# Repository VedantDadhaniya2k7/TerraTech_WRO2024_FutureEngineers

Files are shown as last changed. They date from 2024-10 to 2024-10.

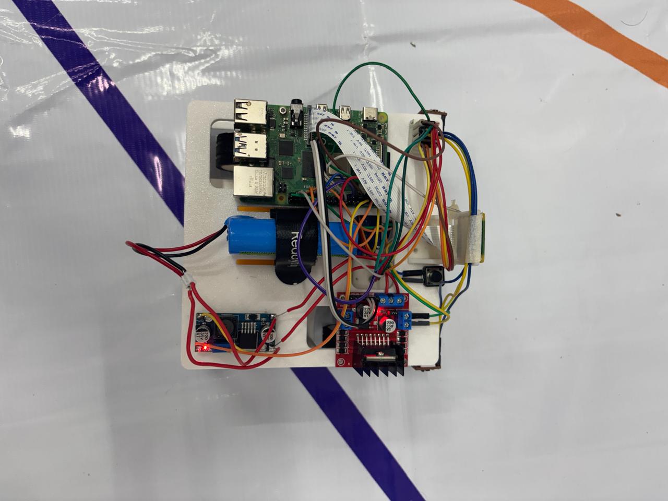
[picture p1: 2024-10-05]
Vehicle_photos/Top_view.jpg

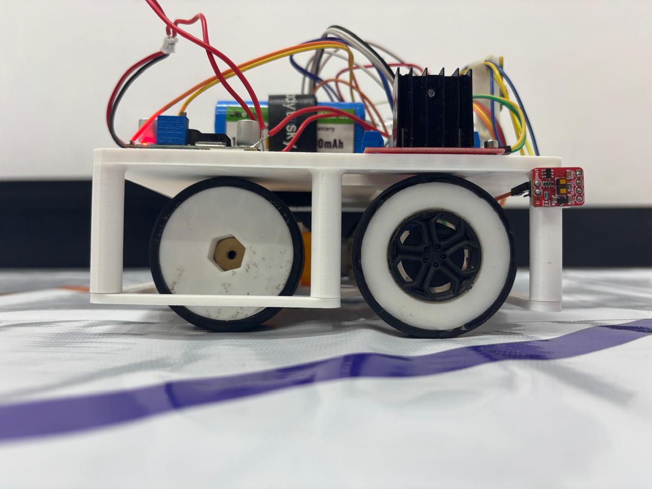
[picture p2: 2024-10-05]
Vehicle_photos/Left_view.jpg

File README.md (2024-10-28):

WRO 2024 Future Engineers - Team TerraTech (Team code: 1844)
====

This repository contains engineering materials of the self-driven vehicle of Team TerraTech participating in the WRO Future Engineers competition in the season 2024.

## Content

* `Documentation` contains an Engineering Document describing our Robot, Its components, Why we selected each Component, Code, and, its implementation.
* `Team_Photos` contains photos of the team (an official one and one funny photo with all team members)
* `Vehicle_Photos` contains photos of the vehicle (from every side, from top and bottom)
* `Video` contains videos that demonstrate the robot's functionality including it completing 3 laps of the Open Challenge
* `Schematics` contains schematic diagrams of each electromechanical components (electronic components and motors) used in the vehicle and how they connect to each other and RaspberryPi and also one schematic with the complete circuit connections shown
* `Source_code` contains code of control software for all components which were programmed to participate in the competition
* `3D_models` contains the files for models used by 3D printers, laser cutting machines and CNC machines to produce the vehicle elements. It contains the files in both STL and gcode format
* `Component_tests` contains code for testing and making sure each component of the whole robot is functional. Includes test codes for servo motor, rear motors, camera recognition, as well as the vl53l1x distance measurement sensor

## Introduction

### Team Introduction


_**Vedant Dadhaniya** (Left Side) - Team Lead, Head of Programming and 3-D Design_

Vedant is a STEM enthusiast who has recurringly been participating in the World Robot Olympiad since 2019 and this is his 4th time participating for it. He began by playing with jigsaw puzzles when he developed interest in LEGO which soon led to introduction to the world of robotics through EV3. Over the years, he has developed many skills in robotics including 3D part designing, electrical wiring, and languages such as Python, C#, HTML/CSS, and Java. He brings his computer vision skills with Raspberry Pi which he had worked on during the COVID Pandemic. He is an avid reader and also likes to play the guitar.

_**Devansh Harivallabhdas** (Right Side) - Head of Hardware and 3-D Printing_ 

Devansh is a Robotics and stem enthusiast from Ahmedabad. It is his first time at World Robot Olympiad. He is 14 and studies in class 9. As a child , Lego building was his favourite activity . He discovered his love for wires , motors and circuits in the Covid lockdown 4 years ago. Ever since he is pursuing it . He also has keen interest in Environmental applications ,Physics and chemistry and a passionate urban farmer. His dream is to create technologies and solutions that can impact the conservation of our environment.

### Reason for choosing the team name _TerraTech_

Terra is Latin for the word earth , since the theme for this WRO is Earth Allies. And Tech as we all know is the shortform of the word technology.

## About the Project

### Open Challenge Working Idea



## How to replicate the robot

First collect all the parts required as mentioned in our [Engineering document](http://bit.ly/3C0usWp)
and print all the parts as given in the `3D_models` folder of this repository

Now assemble all the 3d printed parts and the electromechanical components such that the fundamental component assembly looks like this:

Robot design

Then connect the jumper cables as per the following electrical circuit diagram:

Electrical diagram

Before booting the RaspberryPi 4b, flash a 32GB microSD card with a Bookworm image and insert it into the microSD card slot of the RaspberryPi
Now load the Source code onto the raspberry pi using USB to USB communication or a portable data storage device.

Now in the terminal of the RaspberryPi, setup a virtual environment as such:

```> python3 -m venv <give a name to your virtual environment>```

Activate the virtual environment using the following command:

```> source <name of virtual environment>/bin/activate```

Now install the following libraries using ```> pip install <library name>``` :

* opencv-python
* adafruit-circuitpython-vl53l1x
* board
* digitalio
* numpy

Now the robot is ready to run

# References

* https://learn.adafruit.com/adafruit-vl53l1x/python-circuitpython
* https://learn.sparkfun.com/tutorials/qwiic-distance-sensor-vl53l1x-hookup-guide/python-examples
* https://docs.sunfounder.com/projects/raphael-kit/en/latest/appendix/install_the_libraries.html#create-virtual
* https://docs.sunfounder.com/projects/raphael-kit/en/latest/appendix/i2c_configuration.html#i2c-config
* https://www.youtube.com/watch?v=2bganVdLg5Q&t=42s
* https://github.com/World-Robot-Olympiad-Association/wro2022-fe-template
* https://www.youtube.com/playlist?list=PLGs0VKk2DiYyXlbJVaE8y1qr24YldYNDm

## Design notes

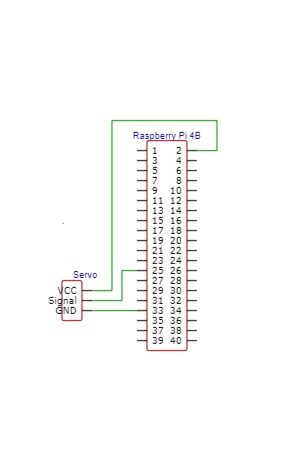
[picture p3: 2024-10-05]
Schematics/Circuit Diagrams/Servo_schematic.jpg

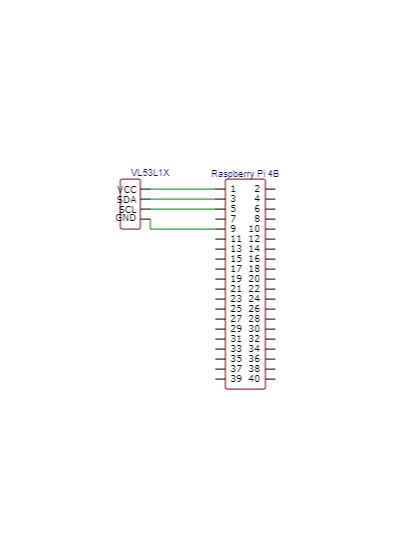
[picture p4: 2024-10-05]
Schematics/Circuit Diagrams/VL53L1X_schematic.jpg

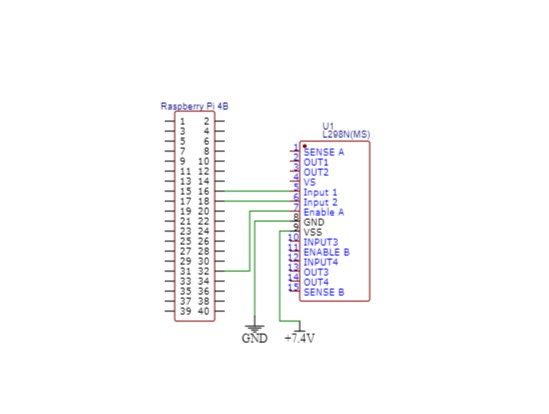
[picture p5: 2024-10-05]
Schematics/Circuit Diagrams/L298N_schematic.jpg

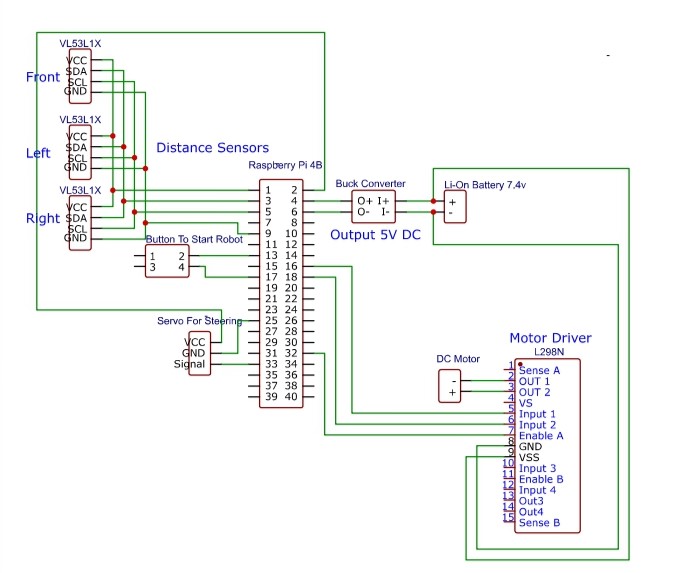
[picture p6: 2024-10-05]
Schematics/Circuit Diagrams/Overall_circuit.jpg

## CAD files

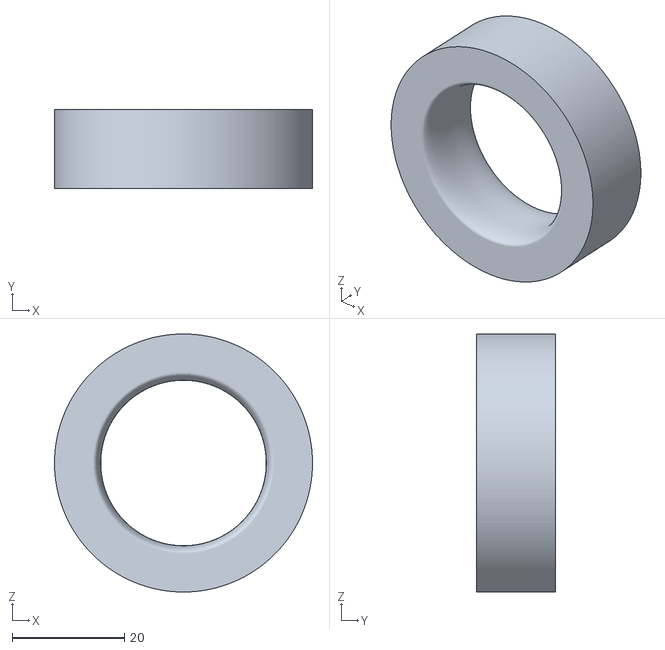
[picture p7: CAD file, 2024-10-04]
3D_models/STL/wheel_front.stl
46.0 x 14.0 x 46.0

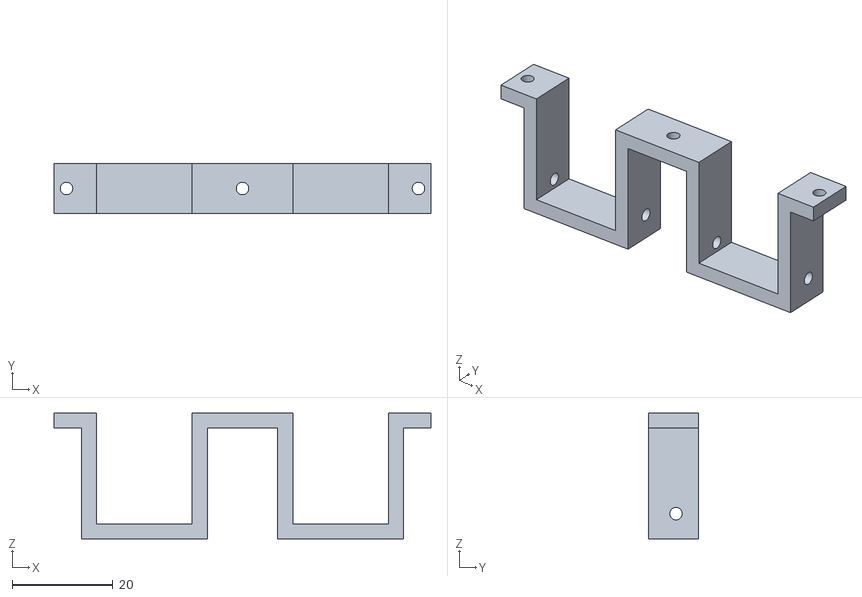
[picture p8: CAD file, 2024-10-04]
3D_models/STL/rear_motor_bracket.stl
75.0 x 10.0 x 25.0

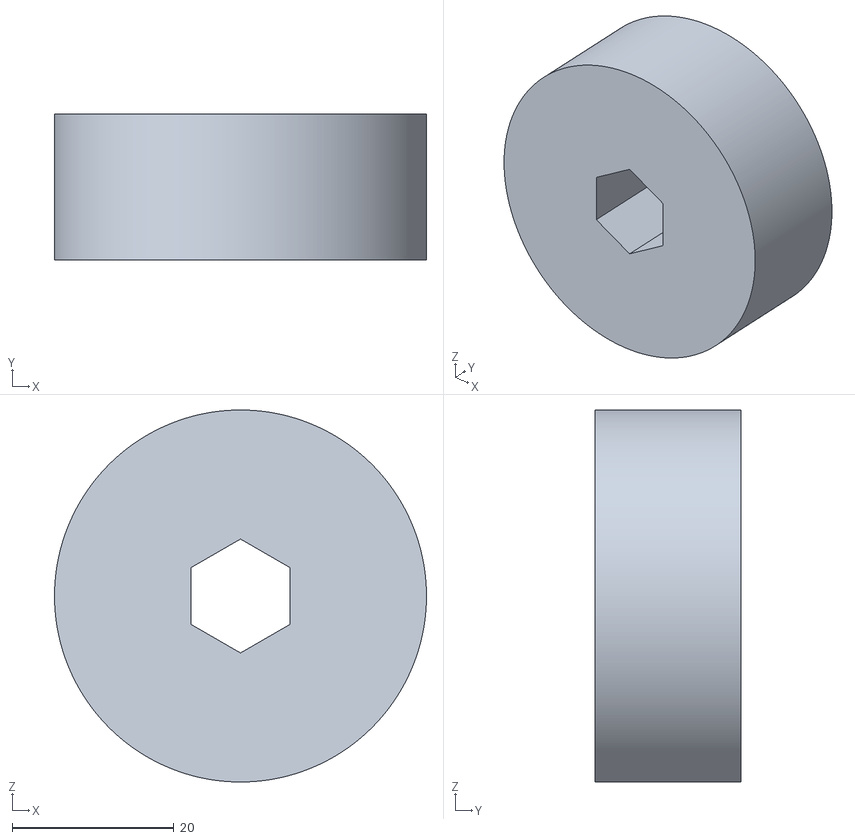
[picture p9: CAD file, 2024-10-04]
3D_models/STL/wheel_rear.stl
46.0 x 18.0 x 46.0

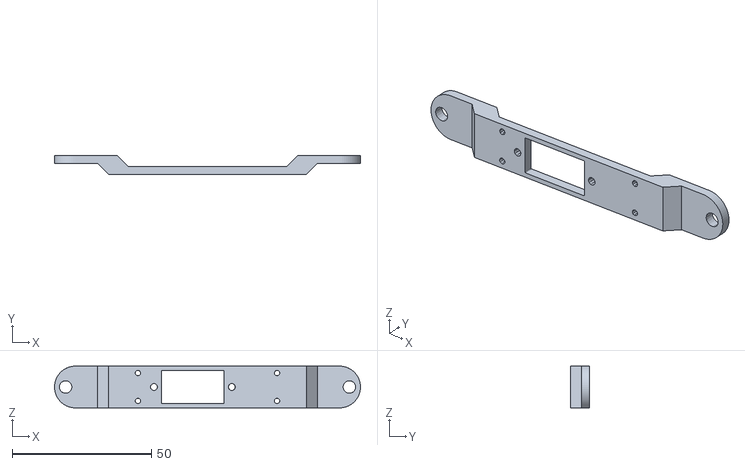
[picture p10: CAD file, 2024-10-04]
3D_models/STL/servo_mount.stl
110.0 x 7.00 x 15.0

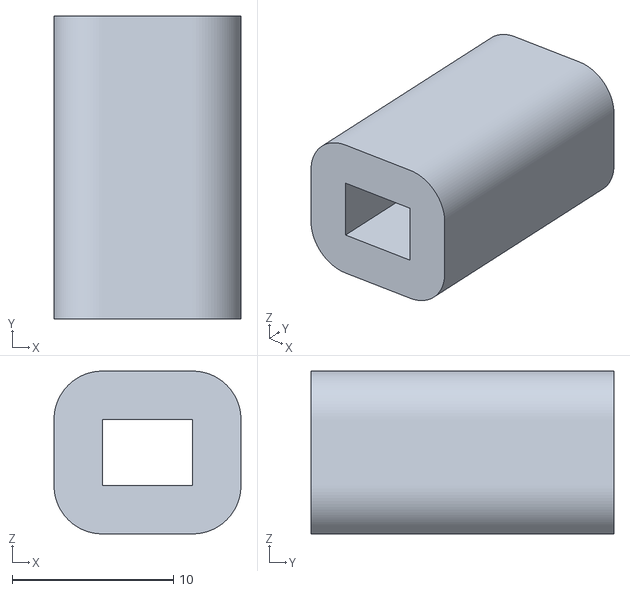
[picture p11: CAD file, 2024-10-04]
3D_models/STL/rear_motor_coupling.stl
11.6 x 18.8 x 10.1

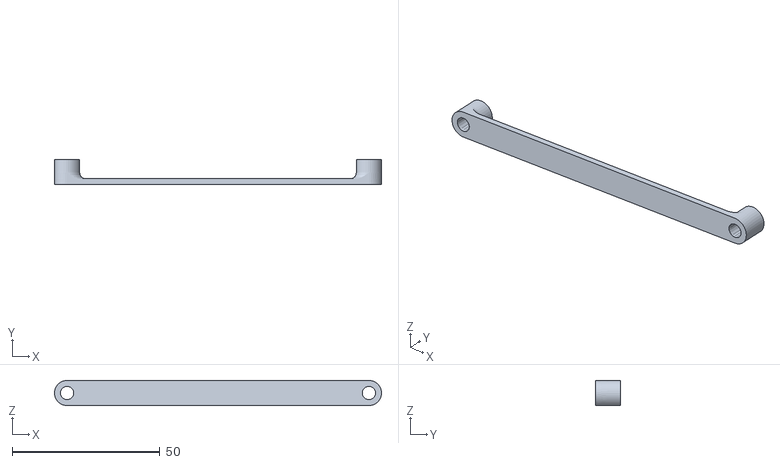
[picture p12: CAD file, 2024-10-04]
3D_models/STL/steering_rod.stl
110.5 x 8.50 x 8.50

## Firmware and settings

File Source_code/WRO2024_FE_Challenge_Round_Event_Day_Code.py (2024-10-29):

"""
Trying to use shape detection to locate red or green block, show the closest one and print() the no. of pillars detected while autosaving the hsv ranges
(P.S. This version of the code is for RaspberryPi not PC)
"""



"""
IMPORTS
"""
import time
time.sleep(5)
import cv2
import math
import numpy as np
from picamera2 import Picamera2
import RPi.GPIO as GPIO
import board
import digitalio
import adafruit_vl53l1x


in1 = 23
in2 = 24
en = 12
servo = 13
SHUT1 = 5
SHUT2 = 6
SHUT3 = 26


"""
GPIO SETUP
"""
GPIO.setwarnings(False)
GPIO.setmode(GPIO.BCM)
GPIO.setup(in1    , GPIO.OUT)
GPIO.setup(in2    , GPIO.OUT)
GPIO.setup(en     , GPIO.OUT)
GPIO.setup(servo  , GPIO.OUT)
GPIO.output(in1   , GPIO.LOW)
GPIO.output(in2   , GPIO.LOW)


motor  = GPIO.PWM(   en, 1000)
servo1 = GPIO.PWM(servo,   50) 
motor.start(100)
motor.ChangeDutyCycle(50)
servo1.start(0)

i2c = board.I2C()
"""
ToF SHUT PIN SETUP
"""
shut_1 = digitalio.DigitalInOut(board.D5 )
shut_2 = digitalio.DigitalInOut(board.D6 )
shut_3 = digitalio.DigitalInOut(board.D26)
shut_1.switch_to_output(value=False)
shut_2.switch_to_output(value=False)
shut_3.switch_to_output(value=False)
"""
ToF SETUP and ADDRESS REASSIGNMENT
"""
#sensor 1
shut_1.value        = True
tof_1               = adafruit_vl53l1x.VL53L1X(i2c)
tof_1.distance_mode = 2
tof_1.timing_budget = 100
tof_1.set_address(0x28)
tof_1.start_ranging()
#sensor 2
shut_2.value        = True
tof_2               = adafruit_vl53l1x.VL53L1X(i2c)
tof_2.distance_mode = 2
tof_2.timing_budget = 100
tof_2.set_address(0x38)
tof_2.start_ranging()
#sensor 3
shut_3.value        = True
tof_3               = adafruit_vl53l1x.VL53L1X(i2c)
tof_3.distance_mode = 2
tof_3.timing_budget = 100
tof_3.set_address(0x48)
tof_3.start_ranging()



"""
Pi Cam Setup
"""
p=Picamera2()

WIDTH = 1280   
HEIGHT = 720

p.preview_configuration.main.size=(WIDTH,HEIGHT)
p.preview_configuration.main.format='RGB888'
p.preview_configuration.align()
p.configure('preview')

p.start()



"""
FUNCTIONS
"""

#* empty fuction
def empty(a):
    pass

#* draws shape and bounding box aroung a countour of sufficient area
def getContours(img, imgContour, clr):
    contours, hierarchy = cv2.findContours(img, cv2.RETR_EXTERNAL, cv2.CHAIN_APPROX_NONE)

    count = 0
    pillars = []
    correct_directions = []

    # draw vert. lines 
    cv2.line(imgContour, (int(WIDTH/3), 0), (int(WIDTH/3), HEIGHT), (0, 255, 255), 1)
    cv2.line(imgContour, (int(2*WIDTH/3), 0), (int(2*WIDTH/3), HEIGHT), (0, 255, 255), 1)
    
    cv2.line(imgContour, ( 291, 720), (679, 419), (0, 255, 255), 1)
    cv2.line(imgContour, (1110, 720), (679, 419), (0, 255, 255), 1)

    for cnt in contours:
        area = cv2.contourArea(cnt)
        area_thresh = cv2.getTrackbarPos("AreaThresh", "Parameters")
        if area >= area_thresh:
            count += 1

            cv2.drawContours(imgContour, cnt, -1, (255, 0, 255), 2)
            
            peri = cv2.arcLength(cnt, True)
            appx = cv2.approxPolyDP(cnt, 0.02*peri, True)
            
            x, y, w, h = cv2.boundingRect(appx) # x: x-coordinate of top left corner of bb, y: y-coordinate of top left corner of bb, w: width , h: height
                
            if y > 355:
                coords = [(x, y), (x+w, y), (x, y+h), (x+w, y+h)]
                pillars.append(coords)
                drawn = False
                
                for i,j in coords:
                    if i < (2*WIDTH/3) and clr == 'green':
                        cv2.rectangle(imgContour, (x, y), (x+w, y+h), (0, 0, 255), 3)
                        drawn = True
                    elif i > (WIDTH/3) and clr == 'red':
                        cv2.rectangle(imgContour, (x, y), (x+w, y+h), (0, 0, 255), 3)
                        drawn = True
                if drawn == False:
                    cv2.rectangle(imgContour, (x, y), (x+w, y+h), (0, 255, 0), 3) 
    
                # area is inversly proporsional to square of dist
                # at 30cm dist -> area = 64000
                dist = 30/math.sqrt(area/32100)
    
                cv2.putText(imgContour, "x: " + str(x) + ', y: ' + str(y) + ', w: ' + str(w) + ', h: ' + str(h), (x, y - 70), cv2.FONT_HERSHEY_COMPLEX, 0.7, (0, 255, 0), 2)
                
                asdfg = (0, 0, 255) if (((((137*(x+w))+(177*(y+h))-167362>0) or (x+w > 679.6))and(clr == 'red')) or ((((-192*(x+w))+(275*(y+h))+15120>0) or (x+w < 679.6))and(clr=='green'))) else (0, 255, 0)
                correct_dir = True if asdfg == (0, 255, 0) else False
                correct_directions.append(correct_dir)
                cv2.putText(imgContour, "Area" + str(int(area)), (x, y - 45), cv2.FONT_HERSHEY_COMPLEX, 0.7, asdfg, 2)
                cv2.putText(imgContour, "Dist" + str(int(dist)), (x, y - 20), cv2.FONT_HERSHEY_COMPLEX, 0.7, asdfg, 2)

    return count, pillars, correct_directions



"""
LOAD MASK DATA
"""
with open('green_mask.txt', 'r') as gm:
    g_hmin, g_hmax, g_smin, g_smax, g_vmin, g_vmax = gm.read().split(' ')

with open('red_mask.txt', 'r') as rm:
    r_hmin, r_hmax, r_smin, r_smax, r_vmin, r_vmax = rm.read().split(' ')

first_round = True
"""
TRACKBARS SETUP
"""
cv2.namedWindow("Green HSV dials")
cv2.resizeWindow("Green HSV dials", 640, 270)
cv2.createTrackbar("HUE Min", "Green HSV dials", int(g_hmin), 179, empty)
cv2.createTrackbar("HUE Max", "Green HSV dials", int(g_hmax), 179, empty)
cv2.createTrackbar("SAT Min", "Green HSV dials", int(g_smin), 255, empty)
cv2.createTrackbar("SAT Max", "Green HSV dials", int(g_smax), 255, empty)
cv2.createTrackbar("VAL Min", "Green HSV dials", int(g_vmin), 255, empty)
cv2.createTrackbar("VAL Max", "Green HSV dials", int(g_vmax), 255, empty)
cv2.createTrackbar("Start detection", "Green HSV dials", 1, 1, empty)

cv2.namedWindow("Red HSV dials")
cv2.resizeWindow("Red HSV dials", 640, 270)
cv2.createTrackbar("HUE Min", "Red HSV dials", int(r_hmin), 179, empty)
cv2.createTrackbar("HUE Max", "Red HSV dials", int(r_hmax), 179, empty)
cv2.createTrackbar("SAT Min", "Red HSV dials", int(r_smin), 255, empty)
cv2.createTrackbar("SAT Max", "Red HSV dials", int(r_smax), 255, empty)
cv2.createTrackbar("VAL Min", "Red HSV dials", int(r_vmin), 255, empty)
cv2.createTrackbar("VAL Max", "Red HSV dials", int(r_vmax), 255, empty)

cv2.namedWindow("Parameters")
cv2.resizeWindow("Parameters", 640, 120)
cv2.createTrackbar("THRESH_2", "Parameters", 10, 255, empty)
cv2.createTrackbar("THRESH_1", "Parameters", 20, 255, empty)
cv2.createTrackbar("AreaThresh", "Parameters", 650, 5000, empty)

btn = 27
led = 16
cmd_given = False
GPIO.setup(led ,GPIO.OUT)
GPIO.setup(btn ,GPIO.IN)
GPIO.output(led  ,GPIO.HIGH)
"""
WAIT FOR BTN ACTIVATION
"""
start= time.time()
print("Awaiting command")
while not cmd_given:
    if GPIO.input(btn) == GPIO.HIGH:
        cur = time.time() - start
    else:
        cur = 0
        start = time.time()
    if cur > 0.5:
        cmd_given = True

GPIO.output(led  ,GPIO.LOW)
time.sleep(1)
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

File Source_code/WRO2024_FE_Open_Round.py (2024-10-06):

import RPi.GPIO as GPIO # type: ignore
import time
import board # type: ignore
import digitalio # type: ignore
import adafruit_vl53l1x # type: ignore

"""
GPIO PINS
"""
btn         = 27
en          = 12
in1         = 23
in2         = 24
servo       = 13
"""
DATA VARIABLES
"""
cur         = 0
lap_counter = 0
turn_dir    = 0
cmd_given   = False
"""
GPIO SETUP
"""
GPIO.setwarnings(False)
GPIO.setmode(GPIO.BCM)
GPIO.setup(in1   ,GPIO.OUT)
GPIO.setup(in2   ,GPIO.OUT)
GPIO.setup(en    ,GPIO.OUT)
GPIO.setup(servo ,GPIO.OUT)
GPIO.output(in1  ,GPIO.LOW)
GPIO.output(in2  ,GPIO.LOW)
GPIO.setup(btn   , GPIO.IN)
"""
PWM SETUP
"""
mpower = GPIO.PWM(en   ,1000)
servo1 = GPIO.PWM(servo,  50) 
"""
I2C SETUP
"""
i2c = board.I2C()
"""
ToF SHUT PIN SETUP
"""
shut_1 = digitalio.DigitalInOut(board.D5 )
shut_2 = digitalio.DigitalInOut(board.D6 )
shut_3 = digitalio.DigitalInOut(board.D26)
shut_1.switch_to_output(value=False)
shut_2.switch_to_output(value=False)
shut_3.switch_to_output(value=False)
"""
ToF SETUP and ADDRESS REASSIGNMENT
"""
#sensor 1
shut_1.value        = True
tof_1               = adafruit_vl53l1x.VL53L1X(i2c)
tof_1.distance_mode = 2
tof_1.timing_budget = 100
tof_1.set_address(0x28)
#sensor 2
shut_2.value        = True
tof_2               = adafruit_vl53l1x.VL53L1X(i2c)
tof_2.distance_mode = 2
tof_2.timing_budget = 100
tof_2.set_address(0x38)
#sensor 3
shut_3.value        = True
tof_3               = adafruit_vl53l1x.VL53L1X(i2c)
tof_3.distance_mode = 2
tof_3.timing_budget = 100
tof_3.set_address(0x48)


"""
WAIT FOR BTN ACTIVATION
"""
start= time.time()
print("Awaiting command")
while not cmd_given:
    if GPIO.input(btn) == GPIO.HIGH:
        cur = time.time() - start
    else:
        cur = 0
        start = time.time()
    if cur > 0.5:
        cmd_given = True
time.sleep(1)
"""
BTN ACTIVATED
"""


"""
START DETECTING
"""
tof_1.start_ranging()
tof_2.start_ranging()
tof_3.start_ranging()
time.sleep(0.1)
d1 = None
d2 = None
d3 = None
while ((d1 == None) or (d2 == None) or (d3 == None)):
	time.sleep(0.1)
	if tof_1.data_ready:
		d1 = tof_1.distance
		print("Sensor 1: ", str( d1 ), end = "         ")
		tof_1.clear_interrupt()
	if tof_2.data_ready:
		d2 = tof_2.distance
		print("Sensor 2: ", str( d2 ), end = "         ")
		tof_2.clear_interrupt()
	if tof_3.data_ready:
		d3 = tof_3.distance
		print("Sensor 3: ", str( d3 ), end = "         ")
		tof_3.clear_interrupt()
	print("")

"""
BEGIN PWM
"""
servo1.start(0)
mpower.start(100)
mpower.ChangeDutyCycle(50)
"""
SET SERVO ANGLE
"""
d = "57"
servo1.ChangeDutyCycle((float(d)/18))
time.sleep(0.5)


if tof_1.data_ready:
	c1 = tof_1.distance
	print("Sensor 1: ", str( c1 ), end = "         ")
	tof_1.clear_interrupt()
if tof_2.data_ready:
	c2 = tof_2.distance
	print("Sensor 2: ", str( c1 ))
	tof_2.clear_interrupt()
time.sleep(0.1)

"""
TURN ON MOTOR
"""
GPIO.output(in1,GPIO.LOW)
GPIO.output(in2,GPIO.HIGH)


while turn_dir == 0:
	time.sleep(0.1)
	if tof_1.data_ready:
		d1 = tof_1.distance
		print("Sensor 1: ", str( d1 ), end = "         ")
		tof_1.clear_interrupt()
	if tof_2.data_ready:
		d2 = tof_2.distance
		print("Sensor 2: ", str( d2 ), end = "         ")
		tof_2.clear_interrupt()
	print("")
	if d1!= None and d1 - c1 > 15:
		turn_dir = 1
		sensor = tof_1
		sleeptime = (1/24)*(c1-25) if c1>25 else 0
	elif d2!= None and d2 - c2 > 15:
		turn_dir = -1
		sensor = tof_2
		sleeptime = (1/24)*(c2-25) if c2>25 else 0
		

servo1.ChangeDutyCycle(0)
GPIO.output(in1,GPIO.LOW)
GPIO.output(in2,GPIO.LOW)
if turn_dir == -1:
	d=80
elif turn_dir == 1:
	d=30
servo1.ChangeDutyCycle((float(d)/18))
time.sleep(0.5)
servo1.ChangeDutyCycle(0)
mpower.ChangeDutyCycle(70)
time.sleep(0.5)
GPIO.output(in2,GPIO.HIGH)
time.sleep(1.55+(turn_dir/20))
GPIO.output(in2,GPIO.LOW)
lap_counter += 1

servo1.ChangeDutyCycle((56/18))
time.sleep(0.3)
servo1.ChangeDutyCycle(0)
mpower.ChangeDutyCycle(60)
time.sleep(0.5)
GPIO.output(in2,GPIO.HIGH)
time.sleep(sleeptime)
GPIO.output(in2,GPIO.LOW)

turning = False
sensor.start_ranging()
time.sleep(0.1)
GPIO.output(in2,GPIO.HIGH)
prev = sensor.distance
sensor.clear_interrupt()
time.sleep(0.1)
while lap_counter < 13:
	time.sleep(0.1)
	if sensor.data_ready:
		dist = sensor.distance
		print("Sensor Of Detected Dir: ", str( dist ), end = '      ')
		sensor.clear_interrupt()
		if dist == None:
			time.sleep(1)
			print("NONE")
			servo1.ChangeDutyCycle((d)/18)
			time.sleep(0.1)
			servo1.ChangeDutyCycle(0)
		elif dist > 36 and prev > 36:
			if turning == False:
				mpower.ChangeDutyCycle(60)
				turning = True
			servo1.ChangeDutyCycle((d)/18)
			time.sleep(0.1)
			servo1.ChangeDutyCycle(0)
			print("Turning")
			prev = dist
		else:
			if turning == True:
				turning = False 
				mpower.ChangeDutyCycle(60)
				lap_counter += 1
			turning = False
			a = 56+(((32-dist)/4 )*6*turn_dir)
			if a > 68:
				a = 68
			elif a < 44:
				a = 44
			servo1.ChangeDutyCycle((a)/18)
			time.sleep(0.1)
			servo1.ChangeDutyCycle(0)
			print("")
			prev = dist
	else:
		print("No data . . . . . . . . . . . . . .. . . . . . ")
		time.sleep(1)
		
time.sleep(1.5)
GPIO.output(in2, GPIO.LOW)

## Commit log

2024-10-04 Component Tests and 3D files
    [rear_motor_bracket.stl, rear_motor_coupling.stl, servo_mount.stl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]
2024-10-05 Schematics upload
